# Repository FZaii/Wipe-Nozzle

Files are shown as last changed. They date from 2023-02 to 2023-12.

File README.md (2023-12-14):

<p align="center">
  <a href="https://space.bilibili.com/1898517">
    
  </a>
    <br />
</p>

<h1 align="center">Wipe Nozzle v2</h1>

*<p align="center">参考Bambu 3D打印机设计的喷嘴擦拭套件
  <br />
  [Nozzle wipe kit designed with reference to Bambu 3D printer]</p>*

**<p align="center">**
**<h3 align="center">喷嘴擦拭套件2.0已上传</h3>**
*<p align="center">反馈意见可以通过[📺BiliBili](https://space.bilibili.com/1898517)私信</p>*

 ---
 
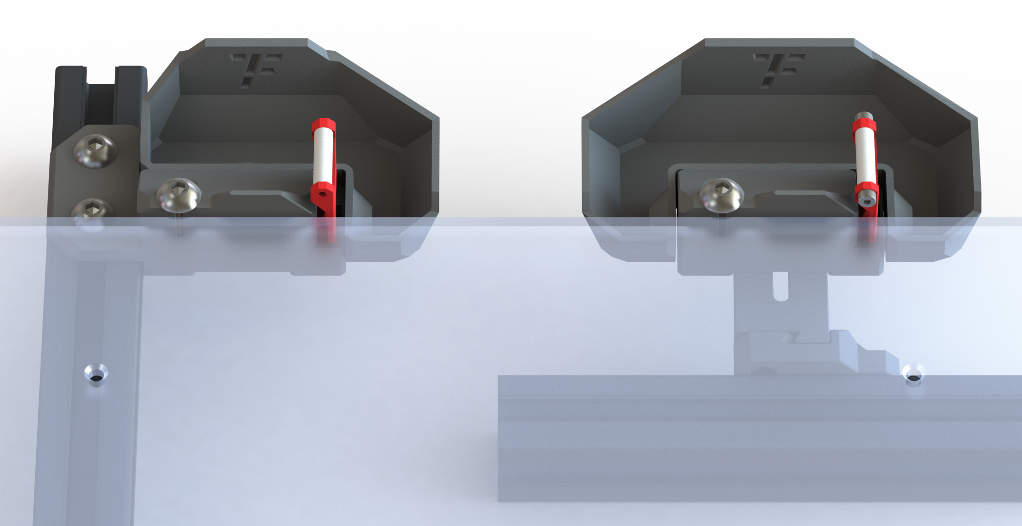
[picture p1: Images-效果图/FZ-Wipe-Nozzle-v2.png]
FZ-Wipe-Nozzle-v2

 
 ---

 ## 目录

- [功能特色](#功能特色)
- [使用提示](#使用提示)
  - [默认安装方式](#默认安装方式)
  - [获取必要参数](#获取必要参数)
- [更新历史](#更新历史)
- [备注](#备注)
  
---

### 功能特色
> - [x] 清洁打印喷嘴
> - [x] 排除热端内余料
> - [x] 多种耗材适用
> - [x] Voron 1 / 2 可用
> - [x] 可换用铜丝刷

### 使用提示

##### 默认安装方式
>  本擦拭套件需要打印机Y轴有至少8mm的空余行程 *(即在Y轴方向，归零点距离热床边缘大于8mm)*，配置文件的默认安装方式如下图 *（如果安装在其他边或者打印头不是归零到最小值，请自行修改宏文件）*
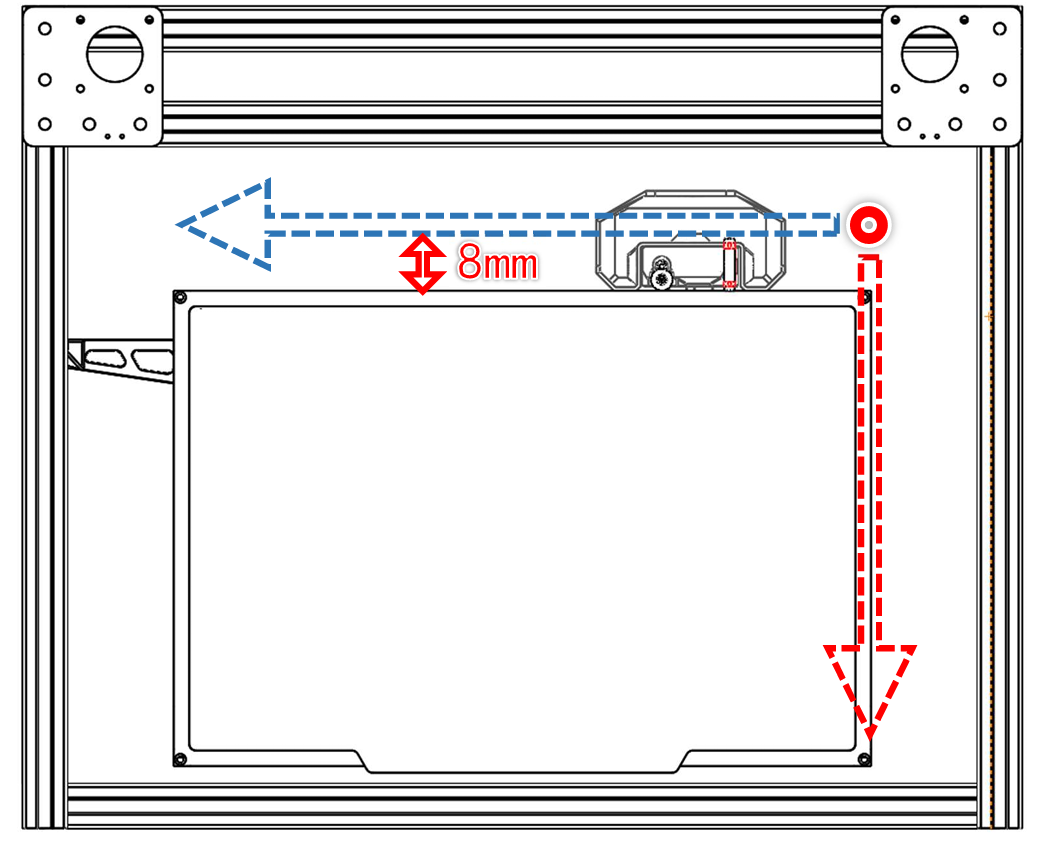
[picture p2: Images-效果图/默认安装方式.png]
默认安装方式
>
  <br />
  
 ##### 获取必要参数
>  将套件固定至热床后，操作喷嘴移动至四氟管的 **前端** 、 **正上方** 、 **并接触** 时，记录X，Y，Z坐标值，填写在 “fz-wipe-nozzle.cfg” 文件对应参数内。
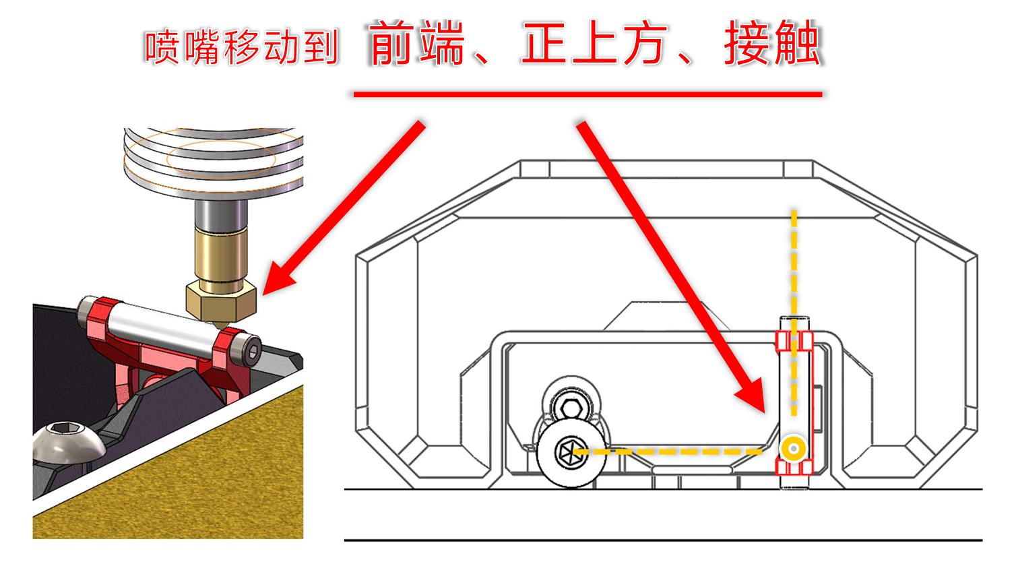
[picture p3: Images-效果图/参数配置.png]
参数配置
>
  <br />

### 更新历史

> **[Ver 2.0]** 2023.12.13 
> - 修改了擦拭臂结构
> - 修改了固定支架，可以两个维度调节
> - 修改了宏文件，将运行过程分为“粘拭喷嘴”、“排除余料”、“擦拭喷嘴”等几个阶段
> - 增加了 Voron 1 / 2 可用的固定方式

> **[Ver 1.0]** 2023.02.17  
> - 修改了宏文件 —— 加快擦拭速度
> - 修改了介绍文档
 
### 备注
- **参考Bambu 3D打印机设计**

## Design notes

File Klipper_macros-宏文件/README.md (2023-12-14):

# Klipper macros
将“fz-wipe-nozzle.cfg”上传至klipper配置文件目录中，并在“printer.cfg”中引用，调用时宏命令为 “WIPE_NOZZLE”

```ini
[include fz-wipe-nozzle.cfg]
```
*printer.cfg引用参考：*

```ini
[gcode_macro PRINT_START]
gcode:
    {% set BED_TEMP = params.BED_TEMP|default(60)|float %}
    {% set EXTRUDER_TEMP = params.EXTRUDER_TEMP|default(210)|float %}
    {% set BED_TEMP_PRE = 50|float %}
    {% set EXTRUDER_TEMP_PRE = 140|float %}

    M104 S{EXTRUDER_TEMP_PRE}       #设置挤出机预热温度
    M140 S{BED_TEMP}                #设置热床打印温度
#    BED_MESH_CLEAR                 #卸载网床
    G28                             #归零3轴
#    Z_TILT_ADJUST                  #Z轴调平
    M109 S{EXTRUDER_TEMP}           #等待挤出机至打印温度
    M190 S{BED_TEMP}                #等待热床至打印温度
    WIPE_NOZZLE                     #擦拭喷嘴
#    CALIBRATE_Z
    G28 Z                           #归零Z轴
    G90                             #所有轴使用绝对定位
    M83                             #挤出机使用相对定位
    G92 E0                          #重置挤出机
#    G1 Y30 F3000
#    BED_MESH_PROFILE LOAD=default   #加载网床
#    M109 S{EXTRUDER_TEMP}           #等待挤出机至打印温度

```

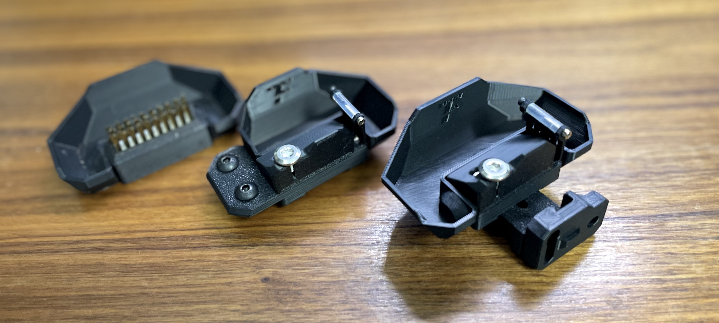
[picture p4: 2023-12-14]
Images-效果图/2种支架、2种清洁方式.jpg

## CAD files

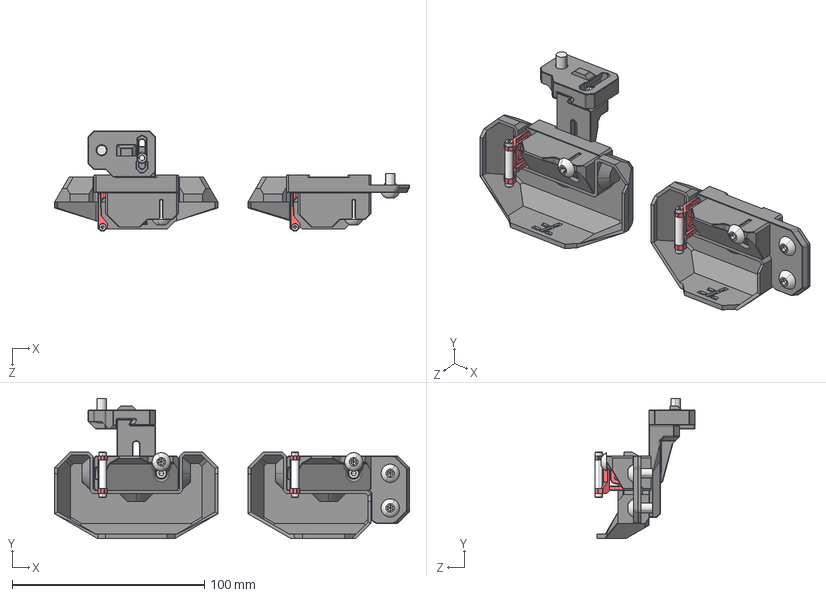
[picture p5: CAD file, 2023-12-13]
CAD-可编辑文件/FZWN_v2.STEP
184.5 x 73.0 x 52.0 mm
FZWN_Block
FZWN_Wipe_Arm x 2
FZWN_Slope x 2
FZWN_Common_Support_Arm
FZWN_Common_Mount
FZWN_Bucket
PTFE_4x15mm x 2
内六角平圆头螺钉 GB-T 70.2-2000 - M5X10-N_GB_SOCKET_TYPE7 M5X10-N x 5
内六角圆柱头螺钉 GB-T 70.1-2000 - M3X8-N_GB_FASTENER_SCREWS_HSHCS M3X8-N x 5
1型六角螺母 GB-T 6170-2000 - M3-N_GB_FASTENER_NUT_SNAB1 M3-N x 2
内六角圆柱头螺钉 GB-T 70.1-2000 - M2X8-N_GB_FASTENER_SCREWS_HSHCS M2X8-N x 4
FZWN_Block-Voron
FZWN_Bucket-Voron

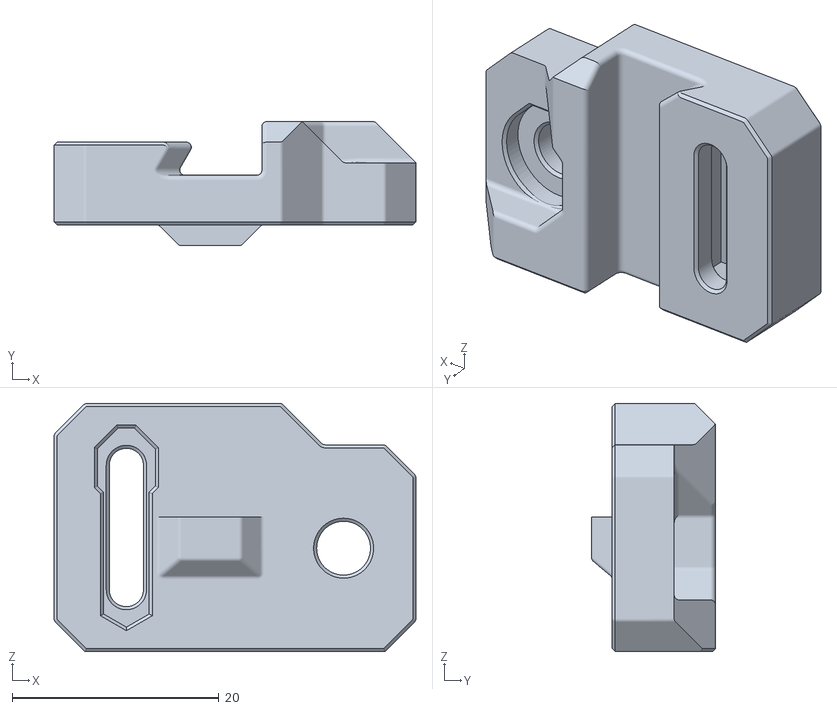
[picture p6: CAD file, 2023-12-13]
STLs-打印文件/5[1]_固定支架_FZWN_Common_Mount.STL
35.0 x 12.0 x 24.0

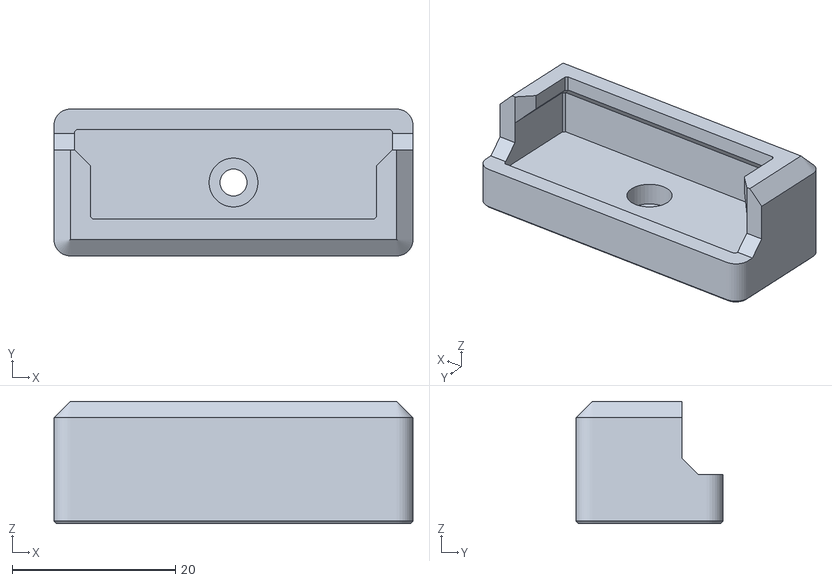
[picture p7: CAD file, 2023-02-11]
STLs-打印文件/可选件/1+2_铜丝刷固定_Brush Holder.STL
44.0 x 18.0 x 15.0

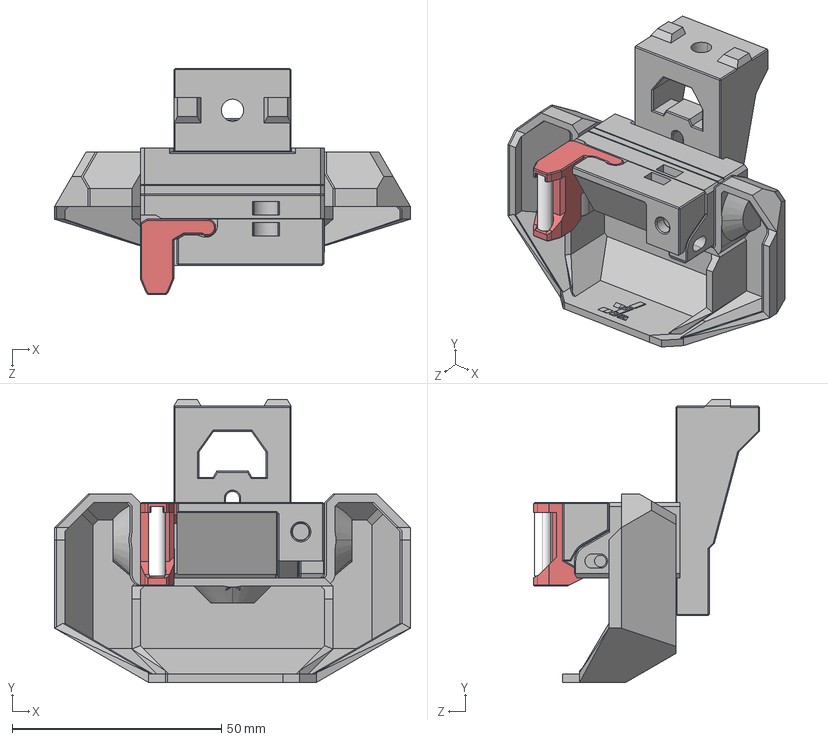
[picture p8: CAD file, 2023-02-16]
CAD-可编辑文件/FZ-WipeNozzle-v1.STEP
85.0 x 67.6 x 54.0 mm
wipe_mount
8mm_block_mount
2mm_extender
wipe_base
wipe_arm
wipe_body
Bucket_Full
Bucket_L
Bucket_R
ｾﾛﾋﾄｷ昮ﾒﾏｩｹﾜ

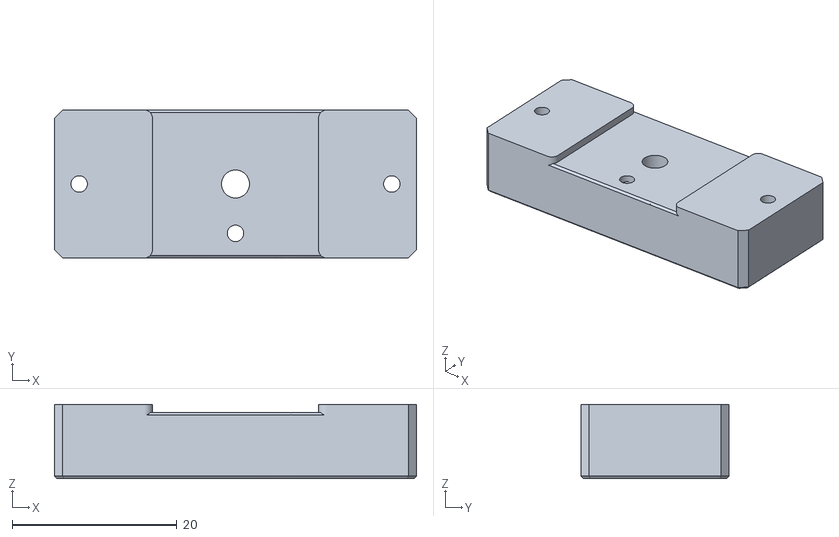
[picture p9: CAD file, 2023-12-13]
STLs-打印文件/3A_连接块_FZWN_Block.STL
44.0 x 18.0 x 9.00

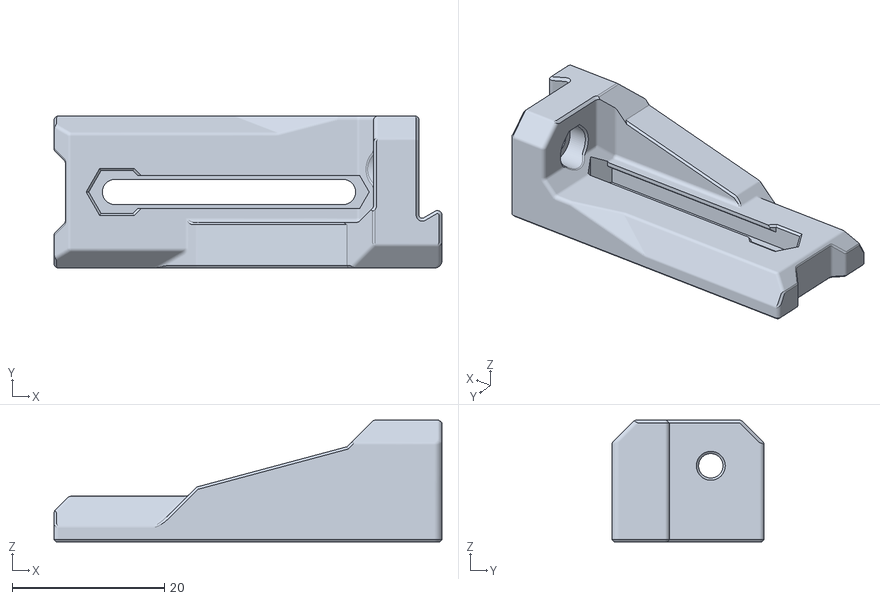
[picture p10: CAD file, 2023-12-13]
STLs-打印文件/5[2]_固定支臂_FZWN_Common_Support_Arm.STL
51.0 x 20.0 x 16.0

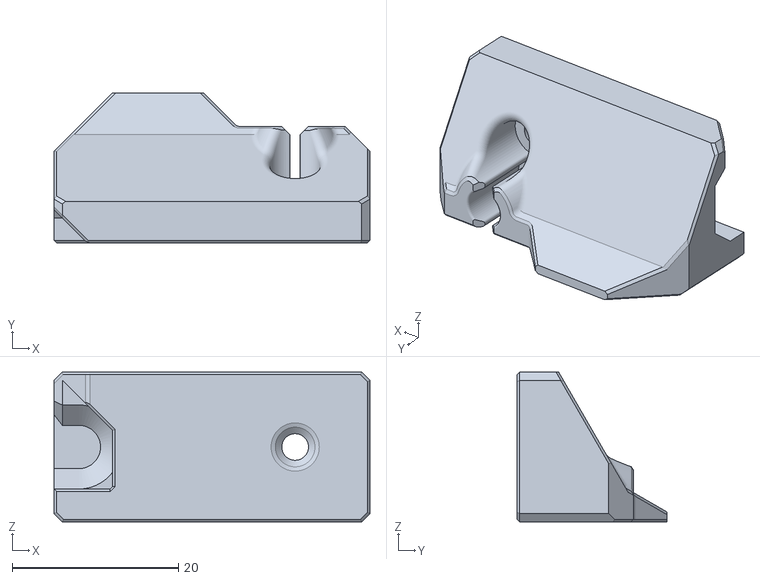
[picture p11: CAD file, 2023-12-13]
STLs-打印文件/2_落料斜坡_FZWN_Slope.STL
38.0 x 18.0 x 18.0

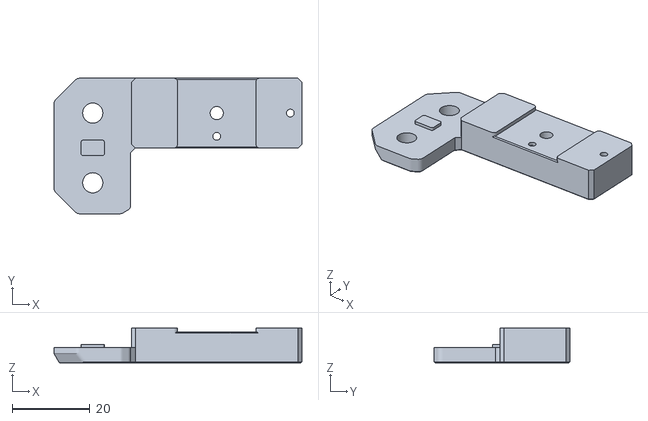
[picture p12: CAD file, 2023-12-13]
STLs-打印文件/3B_Voron连接块_FZWN_Block-Voron.STL
64.0 x 35.0 x 9.00

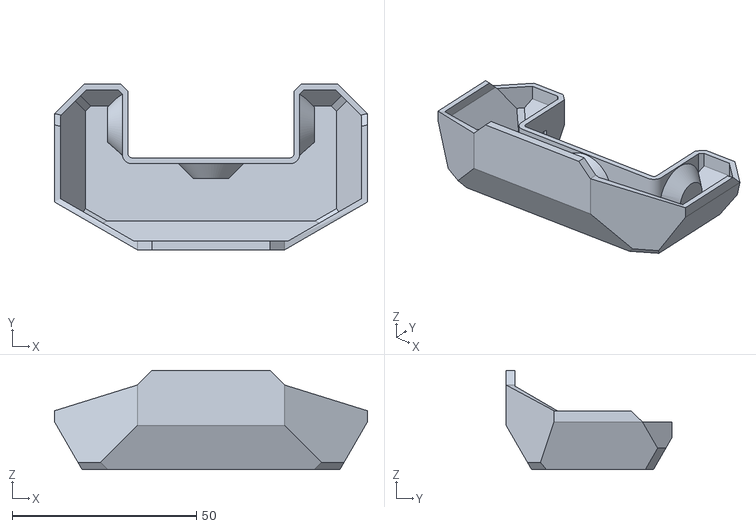
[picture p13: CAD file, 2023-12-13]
STLs-打印文件/4A_废料箱_FZWN_Bucket.STL
85.0 x 45.0 x 27.0

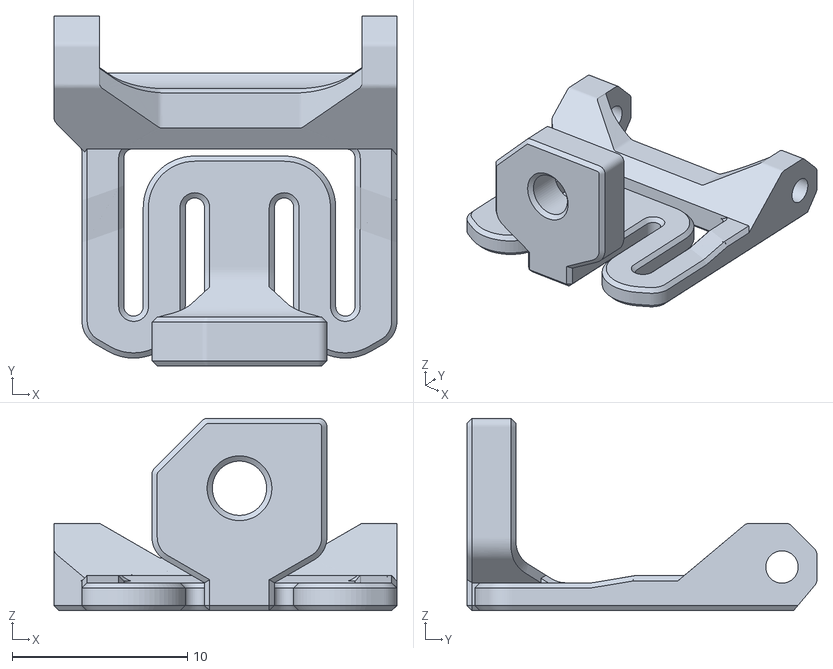
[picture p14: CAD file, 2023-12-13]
STLs-打印文件/1_擦拭摇臂_FZWN_Wipe_Arm.STL
19.6 x 20.0 x 11.0

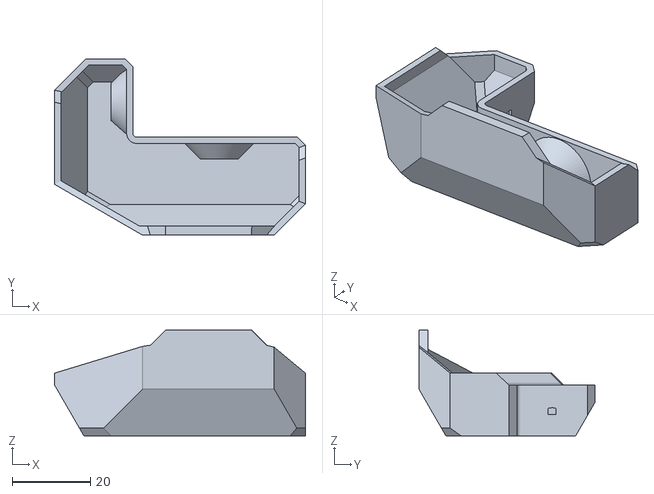
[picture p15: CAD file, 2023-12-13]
STLs-打印文件/4B_Voron废料箱_FZWN_Bucket-Voron.STL
64.0 x 45.0 x 27.0

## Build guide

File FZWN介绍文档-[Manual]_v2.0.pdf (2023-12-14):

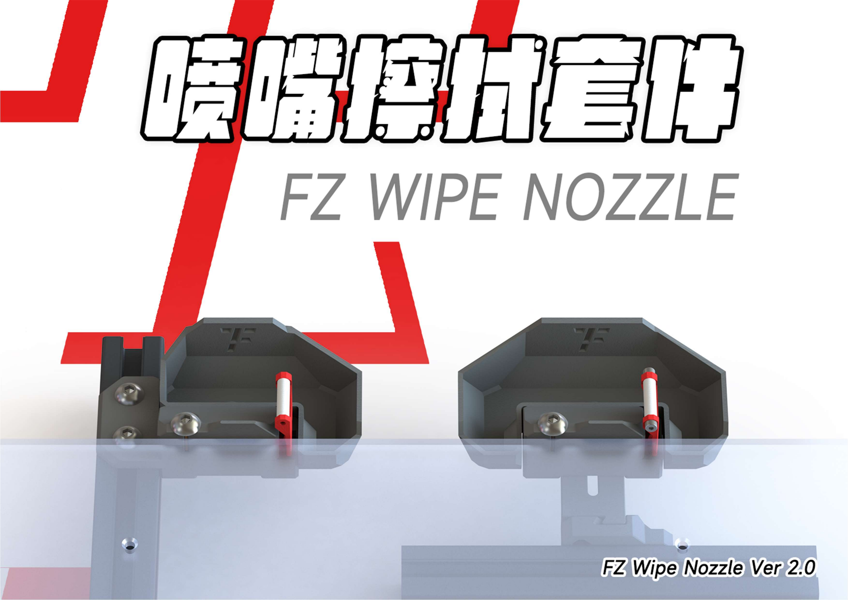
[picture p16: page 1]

FZ WipeNozzzle v2.0

1

FZ WipeNozzzle v2.0

1

# 介绍文档 [Assembly Manual]

# 喷嘴擦拭套件 V2

## 所有件都可以无支撑打印，推荐参数：线宽 0.4mm，层高 0.2mm。

## Github 链接：（stl 文件） 链 接：https://github.com/FZaii/Wipe-Nozzle

## 网 盘 链 接：（stl 文件） 链 接：pan.baidu.com/s/14nzN_thms2-RJVStbM0jaw?pwd=FZWN 提取码：FZWN

## 运 行 过 程： 链 接：https://www.bilibili.com/video/BV1b94y1A7Rv/

# 物料清单 [BOM]

种类 | 型号 | 数量
内六角 | M2x4~8 | 2
| M3x8 | 4
| M5x8 | 2
六角螺母 | M3 | 2
热熔螺母 | M3xΦ5xH4 | 2
圆柱磁铁 | 6x3 | 6
PTFE 聚四氟乙烯管 | 2x4 | 15mm

# 装配要点 [Steps]

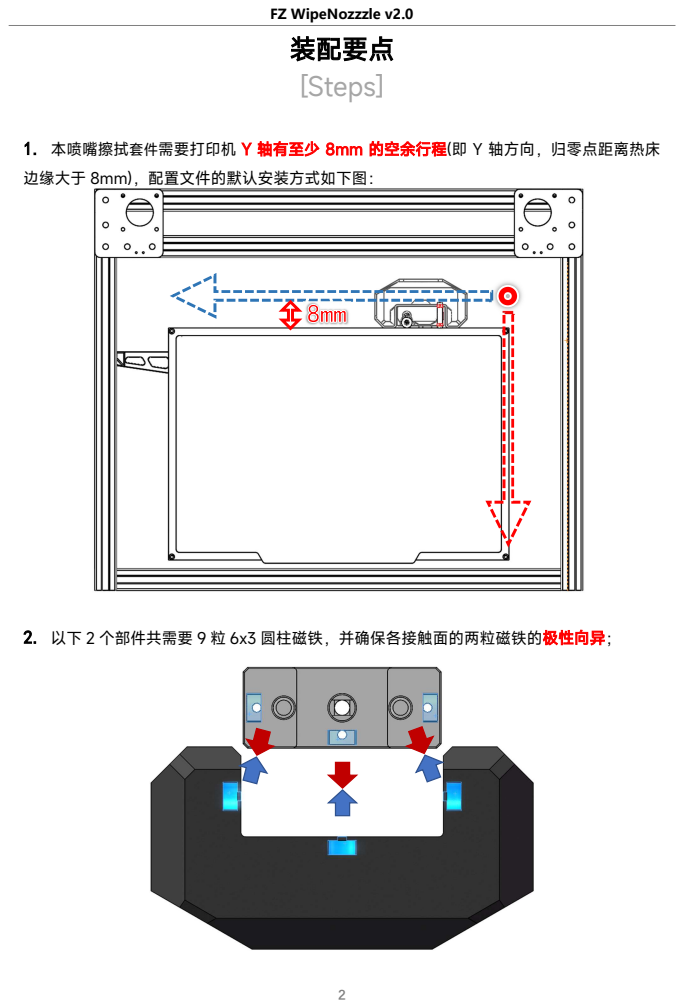
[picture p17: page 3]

1. 本喷嘴擦拭套件需要打印机 Y 轴有至少 8mm 的空余行程(即 Y 轴方向，归零点距离热床
边缘大于 8mm)，配置文件的默认安装方式如下图：

2. 以下 2 个部件共需要 9 粒 6x3 圆柱磁铁，并确保各接触面的两粒磁铁的极性向异；

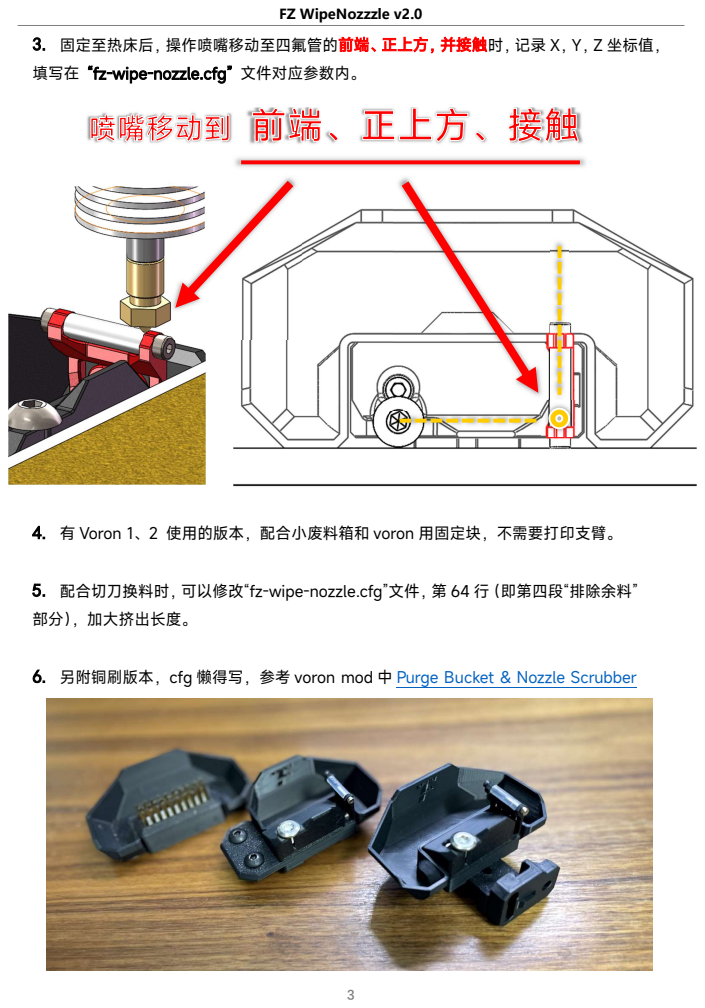
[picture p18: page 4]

3. 固定至热床后，操作喷嘴移动至四氟管的前端、正上方，并接触时，记录 X，Y，Z 坐标值，
填写在 “fz-wipe-nozzle.cfg” 文件对应参数内。

4. 有 Voron 1、2 使用的版本，配合小废料箱和 voron 用固定块，不需要打印支臂。

5. 配合切刀换料时，可以修改“fz-wipe-nozzle.cfg”文件，第 64 行（即第四段“排除余料”
部分），加大挤出长度。

6. 另附铜刷版本，cfg 懒得写，参考 voron mod 中 Purge Bucket & Nozzle Scrubber

4

## Klipper 配置：

将“fz-wipe-nozzle.cfg”上传至 klipper 配置文件目录中，并在“printer.cfg”中引用，调用 时宏命令为 “WIPE_NOZZLE”

## printer.cfg 引用参考：

[include fz-wipe-nozzle.cfg]
[gcode_macro PRINT_START]
gcode:
{% set BED_TEMP = params.BED_TEMP|default(60)|float %}
{% set EXTRUDER_TEMP = params.EXTRUDER_TEMP|default(210)|float %} {% set BED_TEMP_PRE = 50|float %}
{% set EXTRUDER_TEMP_PRE = 140|float %}
| M104 S{EXTRUDER_TEMP_PRE} | #设置挤出机预热温度
| M140 S{BED_TEMP} | #设置热床打印温度
# | BED_MESH_CLEAR | #卸载网床

| G28 | #归零 3 轴
# | Z_TILT_ADJUST | #Z 轴调平

| M109 S{EXTRUDER_TEMP} | #等待挤出机至打印温度
| M190 S{BED_TEMP} | #等待热床至打印温度
| WIPE_NOZZLE | #擦拭喷嘴
# | CALIBRATE_Z

| G28 Z | #归零 Z 轴
| G90 | #所有轴使用绝对定位
| M83 | #挤出机使用相对定位
| G92 E0 | #重置挤出机
| G1 Y30 F3000
# | BED_MESH_PROFILE LOAD=default | #加载网床

# | M109 S{EXTRUDER_TEMP} | #等待挤出机至打印温度

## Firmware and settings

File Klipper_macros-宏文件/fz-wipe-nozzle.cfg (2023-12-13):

# [WIPE NOZZLE]   V2.0    -by:FZai
# !!这个喷嘴擦拭套件需要打印机Y轴有至少8mm的空余行程 (即Y轴原点距离热床边缘大于8mm)
# !!配置参数时请让喷嘴处于四氟管'前端'+'正上方'+'接触时'！！
# 本配置文件总插嘴套件在打印机上安装的位置关系如下图：         
#                    ←X  0
#   ┏━━━━━━━━━━━━━━━━━━┓ Y
#   ┃  ↑8mm↓  [WIPE]   ┃ ↓ 
#   ┃ ┌──────────────┐ ┃                  
#   ┃ │              │ ┃
#   ┃ │     热 床    │ ┃		   
#   ┃ │              │ ┃
#   ┃ └──────────────┘ ┃

[gcode_macro WIPE_NOZZLE]
description: 擦拭喷嘴 -by:FZai V2.0
#请配置以下参数
variable_ptfe_x: 30.0         #喷嘴在四氟管'前端'+'正上方'+'接触时'的X轴坐标
variable_ptfe_y: 6.0          #喷嘴在四氟管'前端'+'正上方'+'接触时'的Y轴坐标
variable_ptfe_z: 2.0          #喷嘴在四氟管'前端'+'正上方'+'接触时'的Z轴坐标
variable_retract_l: 0.4       #正常回抽长度(就是切片软件里填的回抽长度)
variable_safe_z: 8            #挤出头前往擦拭点时的Z轴安全高度
 

#以下参数通常不需要修改
variable_wipe_qty: 2          #擦拭次数
variable_wipe_spd: 150        #擦拭速度
variable_wipe_drop: 1         #擦拭时喷嘴下降距离
variable_retract_m: 1.5       #回抽倍数（若耗材粘性大。可以适度增加该值）
#以下参数不要动！
variable_extrusion_dist: 30.5 #四氟管与M5螺钉中心点的X轴距离


gcode:
  {% if "xyz" not in printer.toolhead.homed_axes %}
   G28
  {% endif %}
 
  G90                         #所有轴使用绝对定位
  M83                         #挤出机使用相对定位
 ##------1.移动到挤出点
  G1 Z{safe_z} F500
  G1 X{ptfe_x + extrusion_dist} Y{ptfe_y} F6000
  G1 Z{ptfe_z - wipe_drop} F500
 ##------2.挤出耗材
  G92 E0              #重置挤出机
  M106 S255           #风扇全开
  G1 E-1 F200
  G1 E10 F300
  G1 E10 F200
  G1 E5 F100
  G4 P500  
  G1 E{ - 0.2 - retract_l * retract_m} F1800  #回抽
  G4 P4000            #驻留 P<毫秒>
  G1 Z{ptfe_z} F500
 ##------3.粘拭喷嘴
 {% for wipes in range(1, (wipe_qty + 2)) %}
   G1 X{ptfe_x + extrusion_dist} Y{ptfe_y - 2} F8000 
   G1 X{ptfe_x + extrusion_dist - 2} Y{ptfe_y} F8000
   G1 X{ptfe_x + extrusion_dist} Y{ptfe_y + 2} F8000
   G1 X{ptfe_x + extrusion_dist + 2} Y{ptfe_y} F8000
 {% endfor %}
  G1 X{ptfe_x + extrusion_dist} Y{ptfe_y - 2} F8000 
 ##------4.排除余料
  G1 X{ptfe_x + 15} Y{ptfe_y - 5} F8000 
  G1 E10 F200         #增大此处挤出数值，可以配合耗材切刀，换料后排除余料          
  G4 P1000
  G1 E{ - 0.4 - retract_l * retract_m} F1800  #回抽
  G4 P4000            #驻留 P<毫秒>
 ##------5.擦拭喷嘴
  G1 Z{ptfe_z - wipe_drop} F500
 {% for wipes in range(1, (wipe_qty + 1)) %}
   G1 X{ptfe_x - 10} F{wipe_spd * 60}
   G4 P200
   G1 X{ptfe_x + 10} F{wipe_spd * 60}
   G4 P500
 {% endfor %}
 ##------6.归位
  G1 Z{safe_z}
  G92 E0
  M107                 #关闭风扇
#  M104 S0             #关闭挤出机加热棒
